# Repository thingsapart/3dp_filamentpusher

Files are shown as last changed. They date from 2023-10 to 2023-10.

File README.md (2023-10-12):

# Filament "Pre-Extruder" for 3D-printers

## Why?

The idea is to overcome the friction in the reverse bowden and spool holder that the main extruder has to work against by pre-feeding the main extruder.

## What is it?

An open-source Klipper-enabled filament-pushing "pre-extruder".

## How?

The implementation is via a bunch of Klipper Macros and "[extruder_stepper]" that's linked to the main extruder.

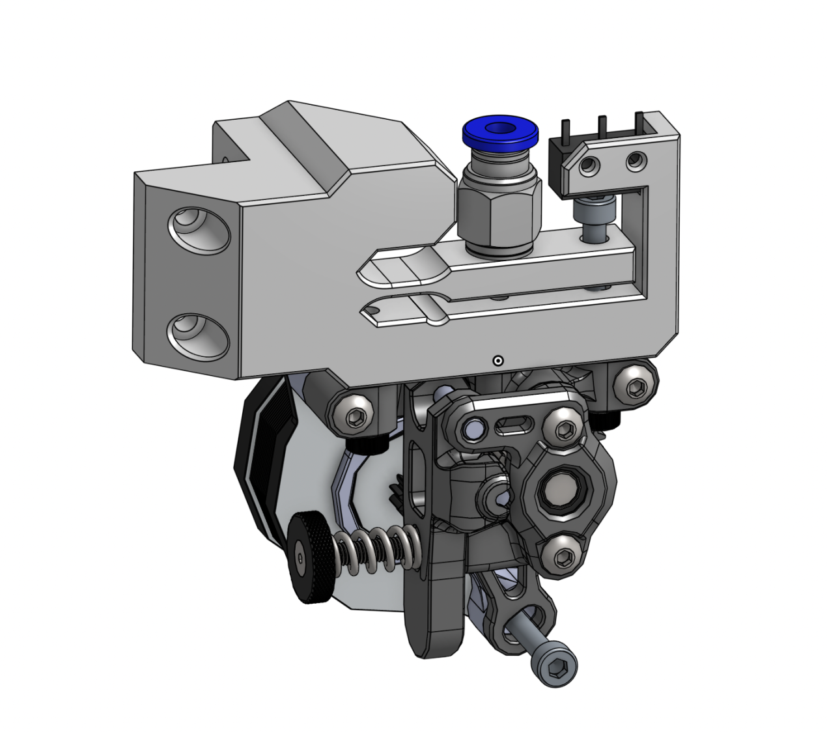
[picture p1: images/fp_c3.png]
3D CAD View


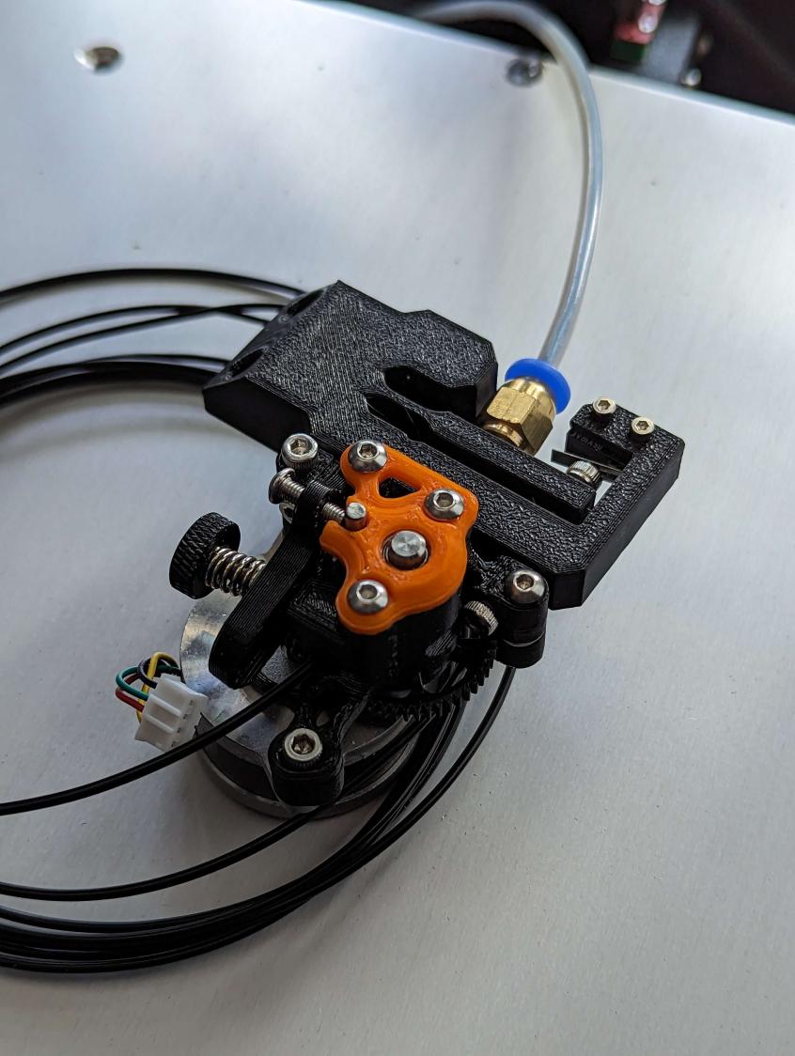
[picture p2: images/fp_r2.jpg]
The assembled pre-feeder proto


The yet-untested main idea is that the pre-feeder extrudes a tad more than the main extruder consumes, thereby creating "pressure" inside the reverse bowden. Then there is in turn a little switch on the pre-feeder and a flexible mechanism and once the pressure reaches a certain level the switch is triggered. That then triggers a Klipper Macro which reduces the rotation distance (thereby reversing the differential speed of the pre-feeder) and reducing the reverse bowden pressure until the switch is released, when the rotation distance is again restored and pressure slowly built up again.

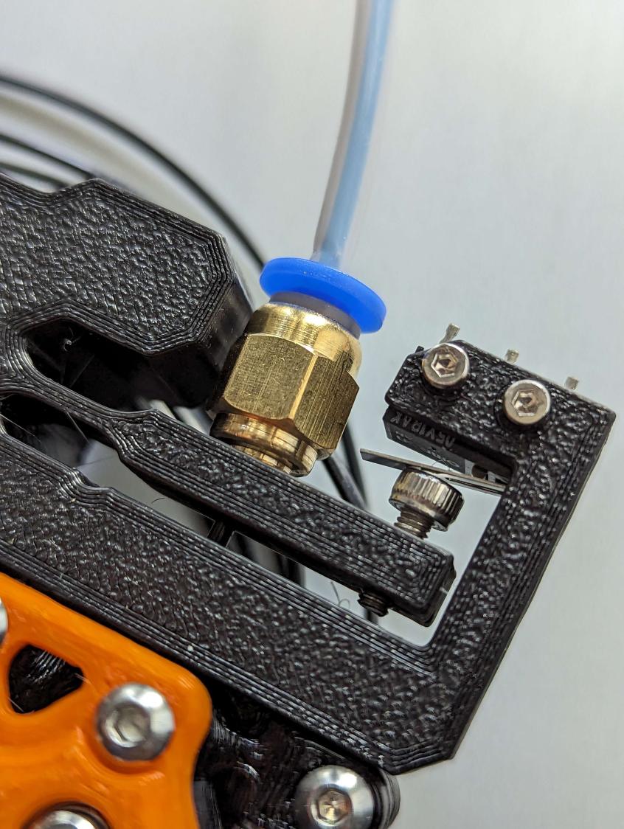
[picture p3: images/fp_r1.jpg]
The switch and spring mechanism


## Video of it working

<div align="center" width="100%" markdown="1">

  Short Video of both extruders extruding (https://youtube.com/shorts/s7kXcfv4JuY "Short Video of both extruders extruding")

</div>

## CAD

The CAD is available here as STEP and [in OnShape](https://cad.onshape.com/documents/6f2557d9a5eb1b365c3bf8f4/w/888f8c00c1b7e363eace9395/e/1c5648967865eb9401f046b9)

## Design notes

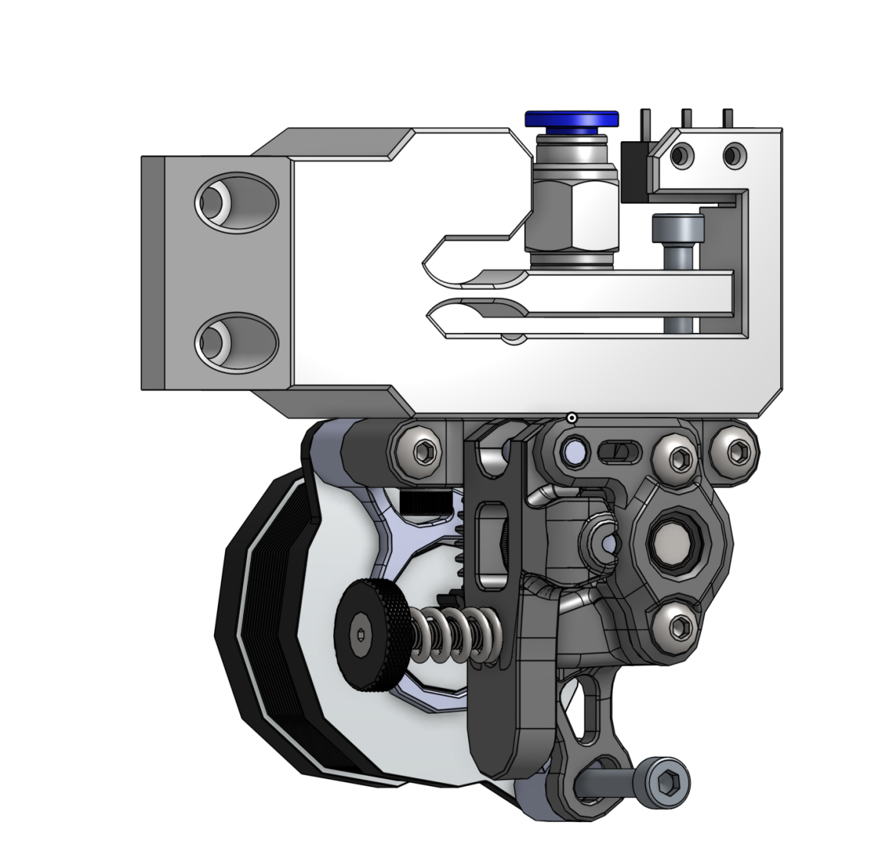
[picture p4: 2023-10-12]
images/fp_c1.png

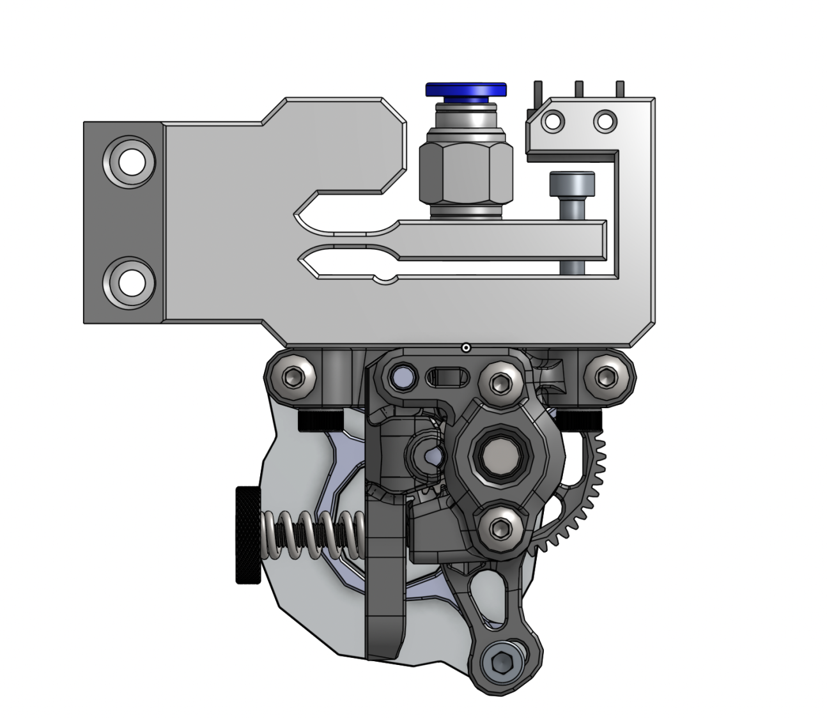
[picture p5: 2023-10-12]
images/fp_c2.png

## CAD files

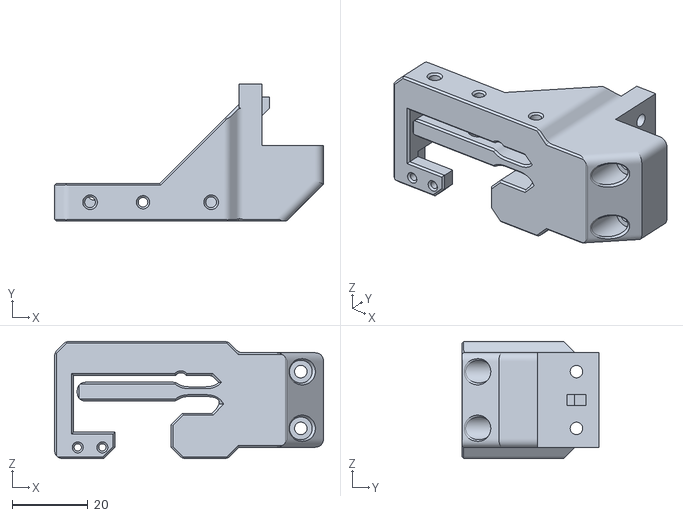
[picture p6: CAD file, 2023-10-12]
stl/Filament Pusher - Base.stl
71.1 x 36.3 x 31.0

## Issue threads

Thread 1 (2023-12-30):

Sometimes klipper not receive the switch changed state and continue to a slower or faster speed

nuplanet, 2023-12-30:
Hi!
Thank you this developed this filament prefeeder - I really happy with the detection method through the PTFE tube <-> filament force.
The only problem with, the running (printing) system sometimes not detect the change of the swich state and makes error by remain too fast or too slow the prefeeder extruder after a while.
Are you experienced this problem?
I use this endstop: https://azurefilm.com/product/endstop-mechanical-limit-switch/
I examined the signal of the endstop with an oscilloscope and not found any electrical problem during work.

For examine or solve the problem I made second switch and just use the ON state on each.
With this cahang It made much less error but one time this system skipped a state change too. :(

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

Do you have any idea?

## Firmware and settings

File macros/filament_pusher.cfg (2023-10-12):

# DON'T FORGET TO INCLUDE THIS FILE IN YOUR MAIN KLIPPER CONFIG SOMEWHERE.

# Configure respond for debugging - might want to disable it on your machine.
[respond]
default_type: echo
default_prefix:

[extruder_stepper filament_pusher]
extruder: extruder

# Motor M8.
step_pin: PA10
dir_pin: !PD15
enable_pin: !PA15

# Sherpa Micro.
microsteps: 16
gear_ratio: 50:10
microsteps: 16
full_steps_per_rotation: 200

# Reduce the rotation_distance of the pre-extruder by ~10%.
#
# Pretending to extrude less than we do actually increases the amount of filament fed by ~10%.
# The idea is that the pre-extruder builds pressure in the reverse bowden which is lowered when the
# integrated switch is activated, see "[gcode_button filament_pusher_slowdown]".
#
# We don't want to the pre-extruder to be slower than the main extruder, the switch is used to
# "bleed" excessive pressure.
rotation_distance: 20.5                           # ~= 22.67895 * 90%

[tmc2209 extruder_stepper filament_pusher]
interpolate: True
run_current: 0.90                                 # LDO 17/20mm need about 0.3-0.4 here, cheap Nema14s more.
uart_pin: PF8
stealthchop_threshold: 1

[gcode_macro FP_MOVE]
gcode:
  SAVE_GCODE_STATE NAME=filapush_move
  SYNC_EXTRUDER_MOTION EXTRUDER='filament_pusher' MOTION_QUEUE=
  FORCE_MOVE STEPPER='extruder_stepper filament_pusher' DISTANCE={params.L|default(20)|float} VELOCITY={params.V|default(10)|float}
  SYNC_EXTRUDER_MOTION EXTRUDER='filament_pusher' MOTION_QUEUE=extruder
  RESTORE_GCODE_STATE NAME=filapush_move

[gcode_macro FP_LOAD]
gcode:
  FP_MOVE L=200

[gcode_macro FP_UNLOAD]
gcode:
  FP_MOVE L=-200

[gcode_macro FILAMENT_PUSHER_DEC]
gcode:
  {% set dist = printer.configfile.config['extruder_stepper filament_pusher'].rotation_distance|float %}
  # RESPOND TYPE=echo MSG="Config dist: {dist}, setting to {dist * 1.15}"
  SET_EXTRUDER_ROTATION_DISTANCE EXTRUDER=filament_pusher DISTANCE={dist * 1.15}

[gcode_macro DEBUG_STEPPERS]
gcode:
  RESPOND TYPE=echo MSG="Config dist: {printer.stepper_enable}"


[gcode_macro FILAMENT_PUSHER_INC]
gcode:
  {% set dist = printer.configfile.config['extruder_stepper filament_pusher'].rotation_distance|float %}
  # RESPOND TYPE=echo MSG="Config dist: {printer['extruder_stepper filament_pusher'].rotation_distance}, setting to {dist}"
  SET_EXTRUDER_ROTATION_DISTANCE EXTRUDER=filament_pusher DISTANCE={dist}

[gcode_button filament_pusher_slowdown]
pin: !PC2                                          # Manta M8P => M6-Stop connector.
press_gcode:
  # M117 Filament pusher reducing motion
  FILAMENT_PUSHER_DEC

release_gcode:
  # M117 Filament pusher increasing motion
  FILAMENT_PUSHER_INC
